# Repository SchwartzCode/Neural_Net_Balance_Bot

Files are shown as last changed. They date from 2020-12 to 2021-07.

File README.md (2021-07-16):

# "Smart" Self Balancing Robot



Using simple neural networks to replicate sensor fusion and dual-loop PID control of a self-balancing robot. The inner PID loop controls the robot's attitude, and the outer controls its translational position. The robot uses an [MPU-6050 IMU](https://www.adafruit.com/product/3886) (gyroscope + accelerometer) for feedback on its attitude and an encoder on one of its wheels for feedback on its position.

## Repository Contents

**CAD_files/** - files used to 3D print robot's body

**components/** - arduino files for testing different components before integrating together

**PID_controller/** - arduino file for dual-loop PID controller

**NN_controller/** - arduino file for neural network(s) controller

**LQR_control_arduino/** - arduino file for LQR controller (currently not working)

**LQR_model.py** - script to generate LQR gains from state dynamics and simulate performance

**NN_angle_predictor.py** - script to train network that predicts robot attiude from sensor readings

**NN_arctangent.py** - script to approximate arctangent with a neural net (sanity checking)

**NN_data_generator.py** - script to generate training data (randomly generates inputs and calculates PID outputs) for angle prediction and controller networks

**NN_PID_controller.py** - script to train controller network

**NN_util_funcs.py** - utiliy functions for neural network training (random batch selection and calculating loss and accuracy)

**NN_weights_saver.py** - saves neural network weights to .txt files for easy copying into .ino files

**pend_bot_LQR_requirements.txt** - run `pip install -r pend_bot_LQR_requirements.txt` in an anaconda environment to install dependencies for LQR python scripts (or just download the packages listed in the file)

## Neural network structures

### Angle Network

Input: \[last angle estimate, acceleration in y, acceleration in x, rotational velocity about x]

Output: \[ New angle Estimate ]

Layers:

* Input \[4]

* Hidden \[6]

* ReLU

* Output \[1]

### Controller Network

Input: \[last angle estimate, rotational velocity about x, current_encoder_reading, last_encoder_reading]

Output: \[ Desired PWM ]

Layers:

* Input \[4]

* Hidden \[10]

* ReLU

* Output \[1]

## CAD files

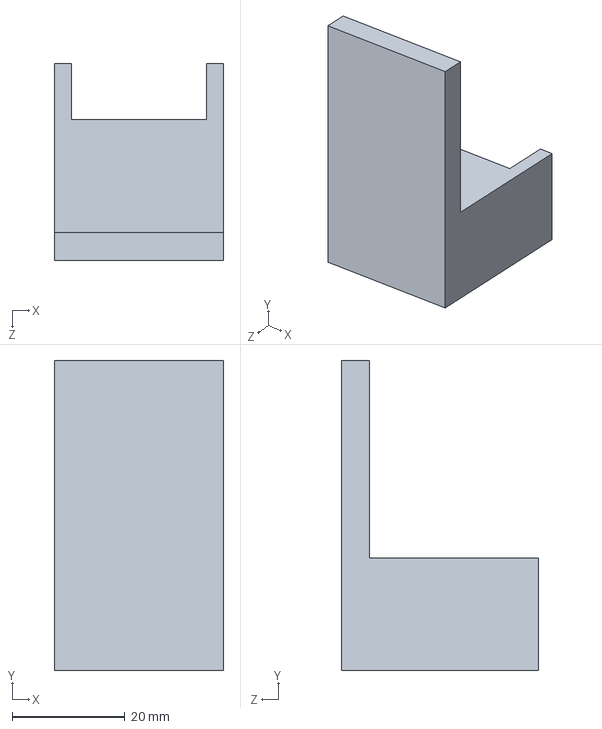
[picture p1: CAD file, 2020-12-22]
CAD_files/motor_supports_rev1.SLDPRT
30.0 x 55.0 x 35.0 mm

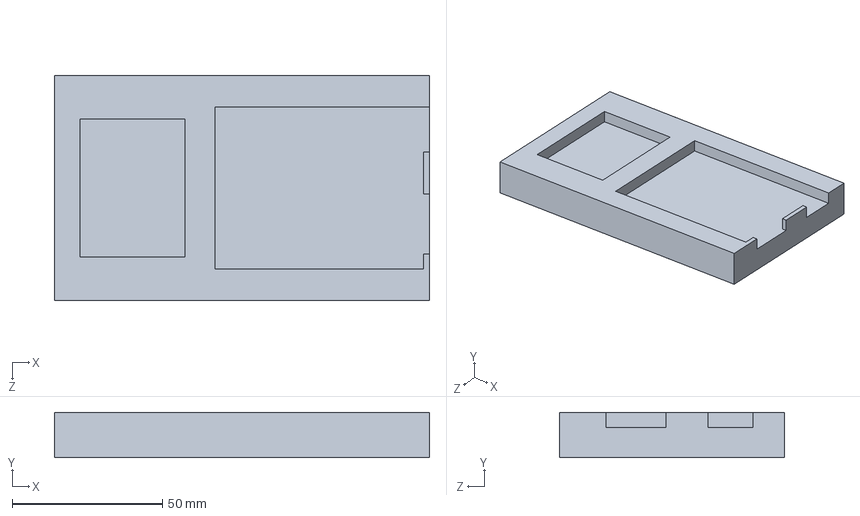
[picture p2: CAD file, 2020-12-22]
CAD_files/base_rev1.SLDPRT
125.0 x 15.0 x 75.0 mm

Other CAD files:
CAD_files/base_rev1.STL
CAD_files/motor_supports_rev1.STL

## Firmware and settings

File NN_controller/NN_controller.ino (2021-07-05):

// Basic demo for accelerometer readings from Adafruit MPU6050

#include <Adafruit_MPU6050.h>
#include <Adafruit_Sensor.h>
#include <MatrixMath.h>
#include <Wire.h>

Adafruit_MPU6050 mpu; //initialize IMU object
// bounds for PWM values - used to clip input to analogWrite()
#define maxPWM  255
#define minPWM  0

#define dt  0.0033 //found empirically, probably a bit off but close enough

// constant used to blend accelerometer & gyroscope angle estimates
//(1-alpha)*angle_gyro
#define alpha  0.01 

// constants for calculating distance travelled from encoder ticks
#define TICKS_PER_REV  1920
#define WHEEL_RADIUS   0.033  // [m]
#define WHEEL_CIRCUMF  0.2073 // [m]

byte newEncoderData = 0;

// initialize variables
float angle = 0.0;

// encoder variables
const byte encoder0pinA = 2;//A pin -> the interrupt pin 0
const byte encoder0pinB = 4;//B pin -> the digital pin 3
byte encoder0PinALast;
int duration = 0;//the number of the pulses
boolean Direction;//the rotation direction

long wheel_pos = 0; // distance travelled by wheel (in encoder ticks)
long wheel_pos_last = 0; // last position of wheels (for calculating d term)
long desired_pos = TICKS_PER_REV * 0.0 / WHEEL_CIRCUMF; //position in ticks to drive robot to (pos initially in m)

// init neural net weights
// initialize matrices for synapse weights and biases
const mtx_type ang_b0[6] = {0.001547, 0.320026, 0.340354, 0.010771, 1.562025, 2.029194};
                                
const mtx_type ang_w0[6][4] = {{0.000343, -0.070401, -1.655140, -0.002654},
                              {-0.009620, -0.214173, 0.294059, 0.002841},
                              {0.026603, -0.230408, -0.318019, 0.000271},
                              {-0.002329, -0.061315, 1.544243, 0.002200},
                              {-0.814444, 0.020287, -0.337145, 0.006185},
                              {-0.225695, 0.027229, 0.540696, 0.012758}};

const mtx_type ang_b1[1] = {0.029889};

const mtx_type ang_w1[6] = {0.701578, 0.119854, -0.109671, -0.754005, -1.482640, 1.128075};

const mtx_type controller_b0[10] = {69.424779, 38.800773, -22.075909, 24.171999, -41.841173, 73.247611, 22.064980, 68.565580, 70.631389, 67.490661};

const mtx_type controller_w0[10][4] = {{-92.130003, -11.383237, 0.001622, 0.003370},
                                        {-1.071874, 0.719454, 0.164862, 0.057819},
                                        {-5.748949, -0.186725, -0.866918, 0.866590},
                                        {-5.235241, -0.098730, -0.847529, 0.847407},
                                        {3.507712, -0.139213, 0.148451, 0.071223},
                                        {101.147043, 8.912909, 0.003575, 0.001770},
                                        {27.889909, -1.397374, 0.020041, 0.042015},
                                        {-89.145994, -9.495121, 0.004560, 0.001643},
                                        {-91.915353, -9.571799, 0.005561, 0.001730},
                                        {-92.772081, -11.135399, 0.003760, 0.004060}};

const mtx_type controller_b1[1] = {5.516958};

const mtx_type controller_w1[10] = {-4.160996, 0.689487, 2.981413, -3.058985, -0.826596, 14.669138, 0.645700, -1.421339, -7.370391, -3.454843};

void setup(void) {

  // open Serial interface
  Serial.begin(115200);

  EncoderInit();
  
  while (!Serial)
    delay(10); // will pause Zero, Leonardo, etc until serial console opens

  // IMU library tries to connect and read data
  Serial.println("Adafruit MPU6050 test!");

  // Try to initialize!
  if (!mpu.begin()) {
    Serial.println("Failed to find MPU6050 chip");
    while (1) {
      delay(10);
    }
  }
  Serial.println("MPU6050 Found!");

  
  // set IMU parameters
  mpu.setAccelerometerRange(MPU6050_RANGE_8_G); // options:  +- 2, 4, 8, 16 [G]
  mpu.setGyroRange(MPU6050_RANGE_500_DEG);      // options:  250, 500, 1000, 2000 [DEG]
  mpu.setFilterBandwidth(MPU6050_BAND_21_HZ);   // options:  260, 184, 94, 44, 21, 10, 5 [Hz]
  Serial.println("");
  delay(100);

  // toggle pins connected to motor controller to output
  pinMode(12, OUTPUT);
  pinMode(13, OUTPUT);
}

/*
 * Initialize encoder pins
 */
void EncoderInit()
{
  Direction = true;//default -> Forward
  pinMode(encoder0pinB,INPUT);
  attachInterrupt(0, readEncoder, CHANGE);
}

/*
 * Interrupt routine for reading encoder data
 */
void readEncoder()
{
//  newEncoderData = PIND;
  int Lstate = digitalRead(encoder0pinA);
  if((encoder0PinALast == LOW) && Lstate==HIGH)
  {
    int val = digitalRead(encoder0pinB);
    if(val == LOW && Direction)
    {
      Direction = false; //Reverse
    }
    else if(val == HIGH && !Direction)
    {
      Direction = true;  //Forward
    }
  }
  encoder0PinALast = Lstate;

  if(!Direction)  wheel_pos++;
  else  wheel_pos--;
}

/*
 *  Read accelerometer and gyroscope data from IMU
 */
double  estimateAngle(){
  /* Get new sensor events with the readings */
  sensors_event_t a, g, temp;
  mpu.getEvent(&a, &g, &temp);

  // correct for IMU offsets (determined experimentally)
  double y_accel = a.acceleration.y + 0.41;
  double z_accel = a.acceleration.z +  1.76;
  double gyro_x = g.gyro.x + 0.05;

  mtx_type angle_inputs[4] = {angle, y_accel, z_accel, gyro_x};

  double new_angle_est = angle_feed_forward(angle_inputs);
  angle = new_angle_est;

  return gyro_x;
}

double estimateAngle_old(){
    /* Get new sensor events with the readings */
  sensors_event_t a, g, temp;
  mpu.getEvent(&a, &g, &temp);

  // correct for IMU offsets (determined experimentally)
  double y_accel = a.acceleration.y + 0.41;
  double z_accel = a.acceleration.z +  1.76;
  double gyro_x = g.gyro.x + 0.05;

  // calculate accelerometer & gyroscope angle estimates
  double angle_accel = atan(y_accel / z_accel);
  double angle_gyro = angle + gyro_x * dt;

  // blend two estimates together
  angle = (1 - alpha) * (angle_gyro) + alpha*angle_accel;

  return gyro_x;
}

double angle_feed_forward(mtx_type inputs[4]){
  mtx_type tmp1[6];
  Matrix.Multiply((mtx_type*)ang_w0, (mtx_type*)inputs, 6, 4, 1, (mtx_type*)tmp1);

  for(int i=0; i<sizeof(tmp1)/sizeof(tmp1[0]); i++){
    tmp1[i] = relu(tmp1[i] + ang_b0[i]);
  }

  mtx_type tmp2[1];
  Matrix.Multiply((mtx_type*)ang_w1, (mtx_type*)tmp1, 1, 6, 1, (mtx_type*)tmp2);

  return tmp2[0] + ang_b1[0];
}

double get_controller_PWM_output(double gyro_x){
  double tmp_angle = (angle + 3.36)/2.5;
//  mtx_type inputs[4] = {tmp_angle, gyro_x, 0.0, 0.0};


  mtx_type inputs[4] = {tmp_angle, gyro_x, wheel_pos, wheel_pos_last};

  mtx_type tmp1[10];
  Matrix.Multiply((mtx_type*)controller_w0, (mtx_type*)inputs, 10, 4, 1, (mtx_type*)tmp1);

  for(int i=0; i<sizeof(tmp1)/sizeof(tmp1[0]); i++){
    tmp1[i] = relu(tmp1[i] + controller_b0[i]);
  }

  mtx_type tmp2[1];
  Matrix.Multiply((mtx_type*)controller_w1, (mtx_type*)tmp1, 1, 10, 1, (mtx_type*)tmp2);

  wheel_pos_last = wheel_pos;

  return tmp2[0] + controller_b1[0];
}

double relu(double input) {
  double output = 0.0;
  if(input < 0.0){
    output = 0.0;
  } else {
    output = input;
  }

  return output;
}

// get sign of a number
template <typename T> int sgn(T val) {
    return (T(0) < val) - (val < T(0));
}


void loop() {

  double st_time = millis();

  double gyro_x = estimateAngle();

//  double NN_PWM = 200*(get_controller_PWM_output(gyro_x) + 3.27);

  double NN_PWM = (get_controller_PWM_output(gyro_x) + 150)/2;

  Serial.println(NN_PWM);

  int outPWM = (int) abs(NN_PWM);

    // clip PWM value at limits of range (0 and 255)
  if (outPWM > maxPWM) {
    outPWM = maxPWM;
  } else if (outPWM < minPWM) {
     outPWM = minPWM;
  } else {
    // no clipping needed, must cast to int though (analogWrite() takes ints)
    outPWM = (int) abs(NN_PWM);
  }

   if(NN_PWM > 0) {
      // we want wheels to move backward
      digitalWrite(12, LOW);
      digitalWrite(13, HIGH);
    } else {
      // we want wheels to move forward
      digitalWrite(12, HIGH);
      digitalWrite(13, LOW);
    }
    // write PWM duty cycle to motors
    analogWrite(3, outPWM);
    analogWrite(11, outPWM);
  
}

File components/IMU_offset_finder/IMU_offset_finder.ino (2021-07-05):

// Basic demo for accelerometer readings from Adafruit MPU6050

#include <Adafruit_MPU6050.h>
#include <Adafruit_Sensor.h>
#include <Wire.h>

Adafruit_MPU6050 mpu; //initialize IMU object
// bounds for PWM values - used to clip input to analogWrite()
uint8_t maxPWM = 255;
uint8_t minPWM = 0;

// used to measure time at beginning and end of each loop
unsigned long currTime = 0;
unsigned long lastTime = 0;
const double dt = 0.0033;

// constant used to blend accelerometer & gyroscope angle estimates
//(1-alpha)*angle_gyro
float alpha = 0.05; 

// initialize variables
float angle = 0.0;
float lastAngle = 0.0;
float I_error = 0.0;

// not used currently but will maybe eventually move gains up here
//float Kp = 75;
//float Ki = 0.0;
//float Kd = 0.0;          

// initialize PID terms 
float P = 0.0;
float I = 0.0;
float D = 0.0;

  
void setup(void) {

  // open Serial interface
  Serial.begin(115200);


  
  while (!Serial)
    delay(10); // will pause Zero, Leonardo, etc until serial console opens

  // IMU library tries to connect and read data
  Serial.println("Adafruit MPU6050 test!");

  // Try to initialize!
  if (!mpu.begin()) {
    Serial.println("Failed to find MPU6050 chip");
    while (1) {
      delay(10);
    }
  }
  Serial.println("MPU6050 Found!");

  mpu.setAccelerometerRange(MPU6050_RANGE_4_G);
  Serial.print("Accelerometer range set to: ");
  switch (mpu.getAccelerometerRange()) {
  case MPU6050_RANGE_2_G:
    Serial.println("+-2G");
    break;
  case MPU6050_RANGE_4_G:
    Serial.println("+-4G");
    break;
  case MPU6050_RANGE_8_G:
    Serial.println("+-8G");
    break;
  case MPU6050_RANGE_16_G:
    Serial.println("+-16G");
    break;
  }
  mpu.setGyroRange(MPU6050_RANGE_500_DEG);
  Serial.print("Gyro range set to: ");
  switch (mpu.getGyroRange()) {
  case MPU6050_RANGE_250_DEG:
    Serial.println("+- 250 deg/s");
    break;
  case MPU6050_RANGE_500_DEG:
    Serial.println("+- 500 deg/s");
    break;
  case MPU6050_RANGE_1000_DEG:
    Serial.println("+- 1000 deg/s");
    break;
  case MPU6050_RANGE_2000_DEG:
    Serial.println("+- 2000 deg/s");
    break;
  }

  mpu.setFilterBandwidth(MPU6050_BAND_21_HZ);
  Serial.print("Filter bandwidth set to: ");
  switch (mpu.getFilterBandwidth()) {
  case MPU6050_BAND_260_HZ:
    Serial.println("260 Hz");
    break;
  case MPU6050_BAND_184_HZ:
    Serial.println("184 Hz");
    break;
  case MPU6050_BAND_94_HZ:
    Serial.println("94 Hz");
    break;
  case MPU6050_BAND_44_HZ:
    Serial.println("44 Hz");
    break;
  case MPU6050_BAND_21_HZ:
    Serial.println("21 Hz");
    break;
  case MPU6050_BAND_10_HZ:
    Serial.println("10 Hz");
    break;
  case MPU6050_BAND_5_HZ:
    Serial.println("5 Hz");
    break;
  }

  Serial.println("");
  delay(100);

  // what information we'll be printing out (for training neural network)
  Serial.println("y_accel | z_accel | gyro_x | I_error | PID_PWM");

  // toggle pins connected to motor controller to output
  pinMode(12, OUTPUT);
  pinMode(13, OUTPUT);
}

void loop() {
  //get time when loop starts
  currTime = millis(); 
  //calculate time since last loop started
  unsigned long elapsedTime = currTime - lastTime; 

  // correct for IMU offsets (determined experimentally)
  double z_accel = 0.0; 
  double y_accel = 0.0; 
  double x_accel = 0.0; 
  double gyro_x = 0.0;

  for(int i=0; i<100; i++){
      
    /* Get new sensor events witthe readings */
    sensors_event_t a, g, temp;
    mpu.getEvent(&a, &g, &temp);

    // update sensor readings
    x_accel += a.acceleration.x - 0.86;
    y_accel += a.acceleration.y + 0.77;
    z_accel += a.acceleration.z +  1.78;
    gyro_x += g.gyro.x + 0.05;
  }

  z_accel /= 100;
  y_accel /= 100;
  x_accel /= 100;
  gyro_x /= 100;
  
  // print values that will be used to train Neural Network
  Serial.println(x_accel);
  Serial.println(y_accel);
  Serial.println(z_accel);
  Serial.println(gyro_x);
  Serial.println("");
}

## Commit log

2020-08-24 Adding all PID controller iterations
2020-08-24 Adding helper arduino files
2020-08-24 Moved some files around, added robot body
    [inverted_pend_body_v4.SLDPRT, inverted_pend_body_v4.STL]
2020-12-22 Adding CAD files
    [base_rev1.SLDPRT, base_rev1.STL, motor_supports_rev1.SLDPRT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]
2020-12-22 deleting some old files
    [inverted_pend_body_v4.SLDPRT, inverted_pend_body_v4.STL]
2020-12-30 Replacing PID controller with a neural network
2021-05-23 Short script to estimate offsets of IMU
    [IMU_offset_finder.ino]
2021-05-27 Tried estimating position from accelerom, seems like offset changes too frequently to do it effectively :/ onto the encoders!
2021-05-28 Encoder mostly working, some funkiness with readings but should be decent enough to work
2021-05-29 Encoder working (with interrupt), need to test with rest of code to see if that will disrupt too much or not
    [encoder_testing.ino]
2021-05-30 Encoder reading works but Arduino is crashing and latching last motor output command after ~10-15 sec of operation
2021-05-30 Wasn't a software error, had too many sensors connected to same ground port on Ard.. whoops!
2021-06-01 Robot drives to positions (and stays pretty darn close to where it converges, seems like convergence is off by ~0.2m though, also will fall over if driving to a point >1m away because it keeps accele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
    [IMU_offset_finder.ino]
2021-06-05 Setting up framework for LQR controlled self-balancing robot
2021-06-05 LQR arduino script structure set
2021-06-05 Added constants for encoder reading conversions to m
2021-06-06 Found another issue with dynamics model, sim is much better real robot still having trouble
    [IMU_offset_finder.ino, LQR_control_arduino.ino]
2021-06-08 So close to balancing on it's own! had to lower alpha in complementary filter 0.05 -> 0.005
2021-06-10 LQR works with USB cord in, doesn't without. Out of ideas for the time being
    [LQR_control_arduino.ino]
2021-06-19 Looks like arctan shouldn't be a problem. Think the issue was I forgot to pass angle from last time step to the network
    [IMU_offset_finder.ino]
2021-06-19 Trained small NN to replicate the PID controller fairly well
2021-06-25 Angle prediction looks good, added printing of seed. Will need to run several iterations to get an ideal seed
2021-06-29 Training a separate network for angle and PWM output seems to work a lot better. Think the MSE loss was getting stuck between the two
2021-07-04 Set up NN on arduino but performance is bad
2021-07-05 Found some problems but NN controller still sucks
    [IMU_offset_finder.ino]
2021-07-05 Creating repo
    [base_rev1.SLDPRT, base_rev1.STL, motor_supports_rev1.SLDPRT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]
